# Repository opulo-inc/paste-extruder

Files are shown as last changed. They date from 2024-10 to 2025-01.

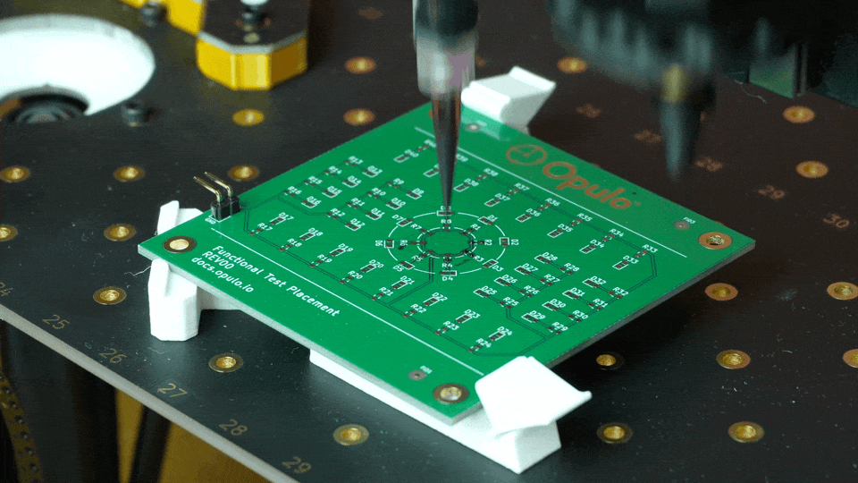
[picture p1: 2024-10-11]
img/hero.gif

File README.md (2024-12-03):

# LumenPnP Paste Extruder

This repository contains the source for a prototype paste extruder head for the LumenPnP.

paste extrusion

**This is a prototype design. It is still in development.**

This extruder head is designed for solder paste and ink dispensing applications. It quickly and easily replaces the right toolhead on any version LumenPnP. It has been used to apply conductive ink and Loctite GC-10 solder paste onto PCBs.

Controlling this toolhead is currently done using `leash`, a python libary for interfacing with the LumenPnP, which can be found [here](https://github.com/opulo-inc/leash). There's an example script in `./sw/extrude/extrude.py` that you can use as a starting point for your own application.

The source CAD for the extruder is designed as a replacement left nozzle. However, the extruder requires a slightly different build of firmware that forces Z homing to occur at a different position, because otherwise the paste extruder will collide with `front-left-leg`. To prevent the extra step of flashing new firmware, the design is mirrored and intended mainly to be used as a replacement *right* nozzle (opposite from the images and YouTube video about this toolhead). If exporting the 3D models yourself, be sure to mirror `extruder-base` and `cartridge-clamp` in your slicer before printing. All other models can be used normally.

## Parts

| Item | Quantity |
| ---- | --- |
| [M3 Nut](https://www.mcmaster.com/90591A250/) | 1 |
| [M3 Threaded Rod](https://www.mcmaster.com/94595A215/) | 1 |
| [Nema 11 Stepper Motor (The higher current rating the better)](https://www.amazon.com/s?k=nema+11+stepper+motor) | 1 |
| [M2.5x5mm Socket Head Bolt](https://www.mcmaster.com/91290A100/) | 4 |
| [M3 Square Nut](https://www.mcmaster.com/97259A101/) | 1 |
| [M3x20mm Socket Head Bolt](https://www.mcmaster.com/91290A123/) | 1 |
| [3ml Luer Lock Syringe](https://www.mcmaster.com/7510A42/) | 1 |
| [Luer Lock Tip (size depends on application)](https://www.mcmaster.com/products/needles/fitting-connection~luer-lock/dispensing-tips-with-luer-lock-connection/tip-type~tapered/) | 1 |

## Install

Installation and setup instructions can be found in this video:

(https://youtu.be/N_p62_QUoKI)

## Help

Feel free to hop in the [LumenPnP Discord Server](https://discordapp.com/invite/TCwy6De ) to help debug and troubleshoot using the extruder head. Also, please feel free to add Github Issues on this repository if you discover any problems.

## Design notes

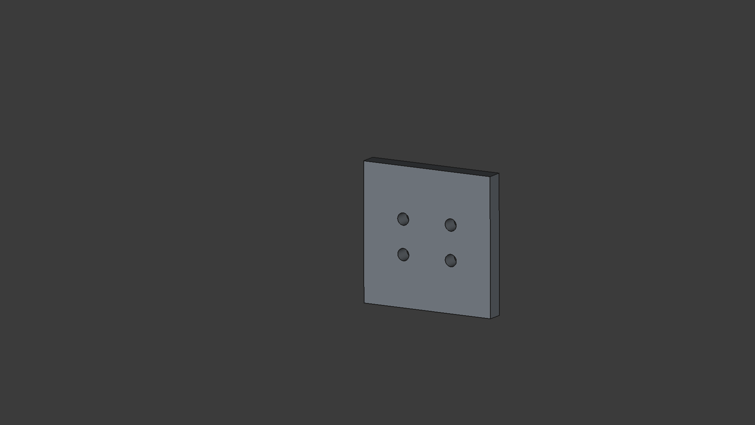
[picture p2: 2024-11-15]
cad/FDM/extruder-base.gif

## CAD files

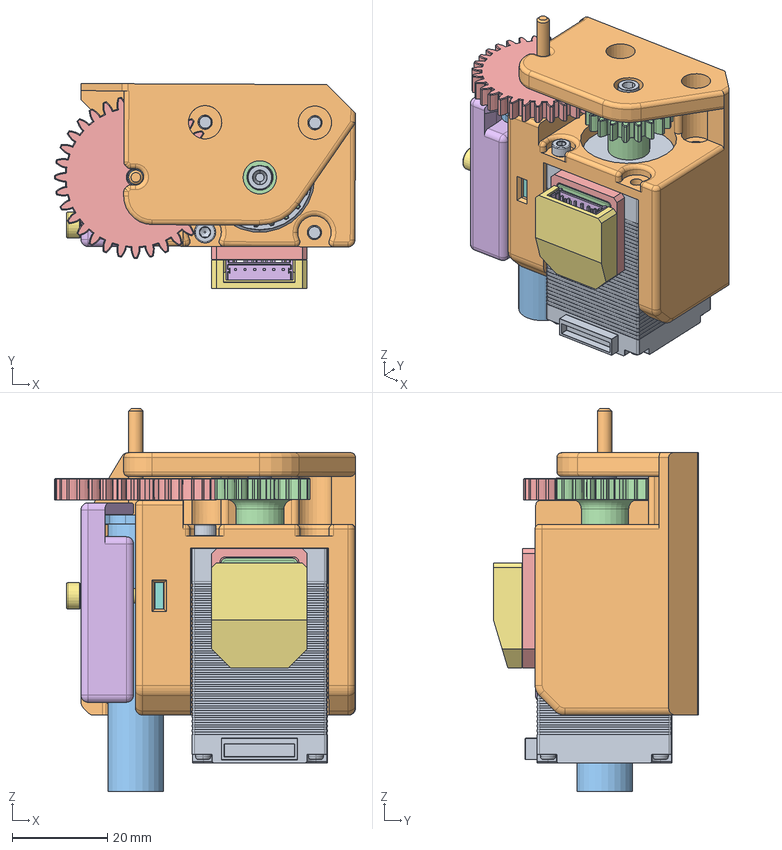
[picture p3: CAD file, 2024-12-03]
cad/subassembly.FCStd
63.1 x 42.9 x 80.2 mm
nema11_001
extruder-base_001
luer_001
extruder-gear_001
cartridge-gear_001
cartridge-clamp_001
M3x20-Screw
M3-Nut
M2.5x5-Screw
M3x70-ThreadedRod
M3-Nut001
stepper-adapter-PCB_001
adapter-mount_001
adapter-cover_001

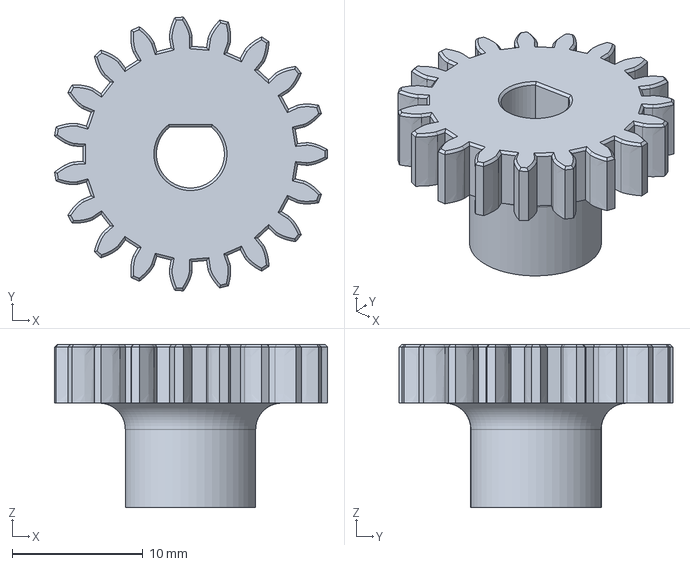
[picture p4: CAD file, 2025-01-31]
cad/FDM/extruder-gear.FCStd
20.9 x 21.0 x 12.5 mm

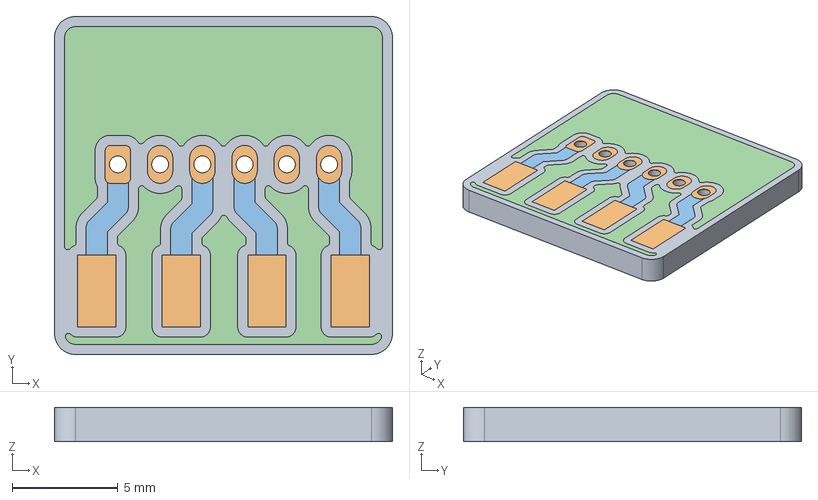
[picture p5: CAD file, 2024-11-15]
cad/OTS/stepper-adapter-PCB.FCStd
16.0 x 16.0 x 1.64 mm
Pcb_5beb
topPads_5beb
topTracks_5beb
topZones_5beb
botPads_5beb
botZones_5beb

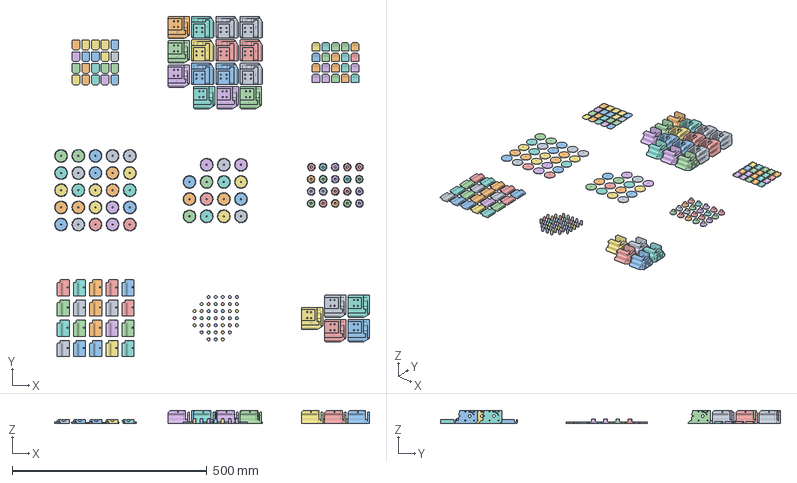
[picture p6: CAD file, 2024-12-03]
mfg/20x-right.3mf
809.3 x 874.3 x 34.0 mm
extruder-base-Body.step x 20
adapter-cover-Body.step x 20
adapter-mount-Body.step x 20
plunger-Body.step x 40
cartridge-clamp-Body.step x 20
extruder-gear-Body.step x 20
cartridge-gear-Body.step 38 x 40

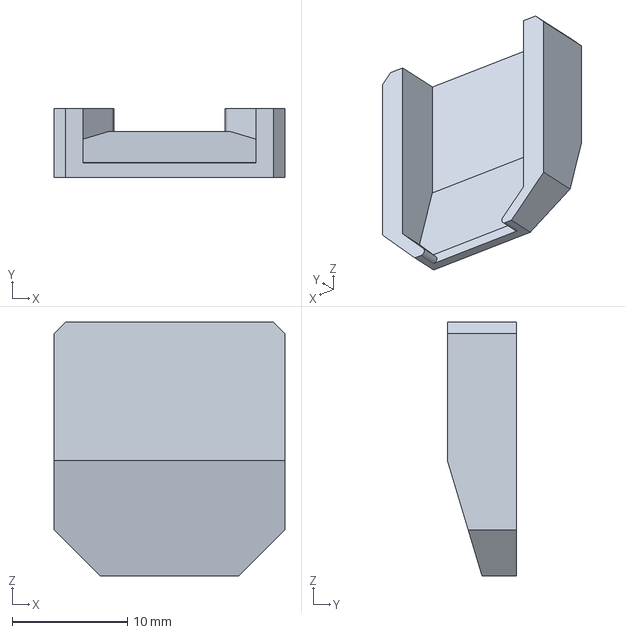
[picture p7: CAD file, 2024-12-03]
cad/FDM/adapter-cover.FCStd
20.0 x 6.00 x 22.0 mm

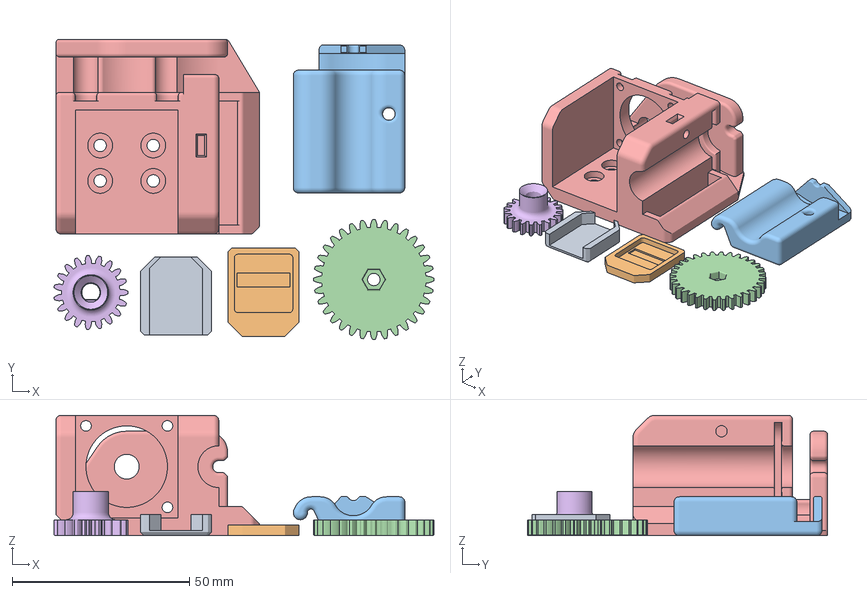
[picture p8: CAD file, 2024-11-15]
mfg/1x-right.3mf
107.3 x 84.8 x 34.0 mm
adapter-cover-Body.step
adapter-mount-Body.step
cartridge-clamp-Body.step
cartridge-gear-Body.step
extruder-base-Body.step
extruder-gear-Body.step

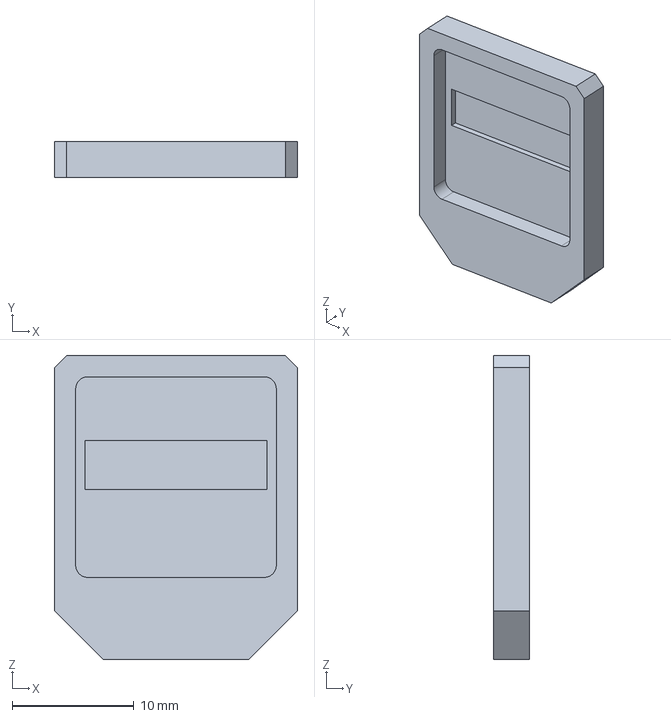
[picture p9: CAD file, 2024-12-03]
cad/FDM/adapter-mount.FCStd
20.0 x 3.00 x 25.0 mm

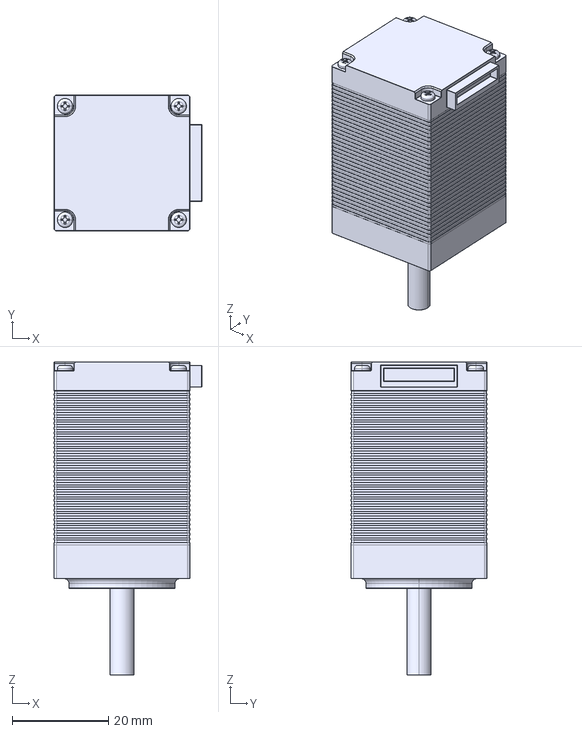
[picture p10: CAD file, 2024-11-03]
cad/OTS/nema11.FCStd
30.7 x 28.2 x 65.0 mm

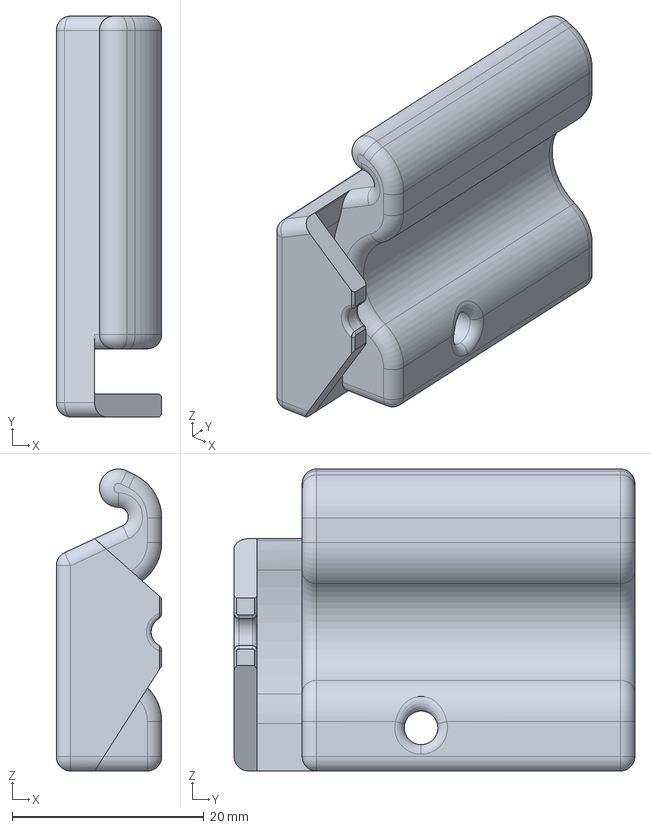
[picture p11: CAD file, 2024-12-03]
cad/FDM/cartridge-clamp.FCStd
11.0 x 41.8 x 31.5 mm

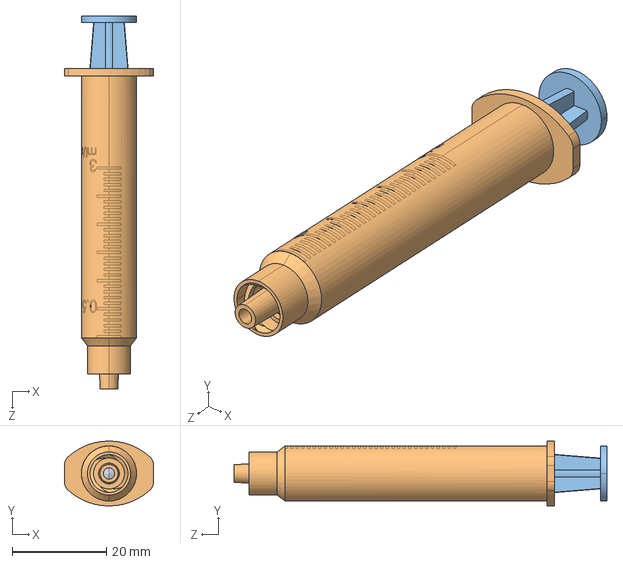
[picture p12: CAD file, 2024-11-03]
cad/OTS/3ml-luer-7510A42.step
18.9 x 13.8 x 79.1 mm

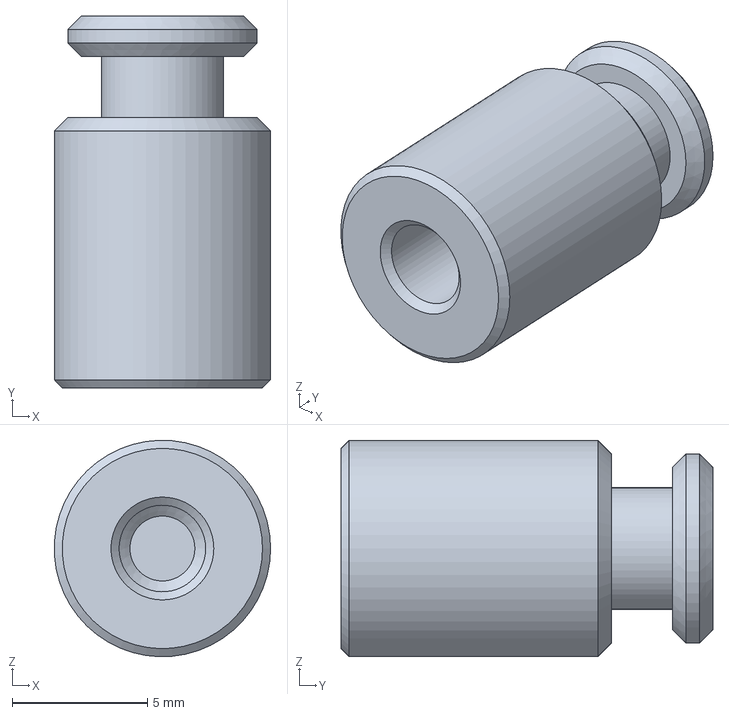
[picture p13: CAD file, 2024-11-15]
cad/FDM/plunger.FCStd
7.99 x 13.8 x 8.00 mm

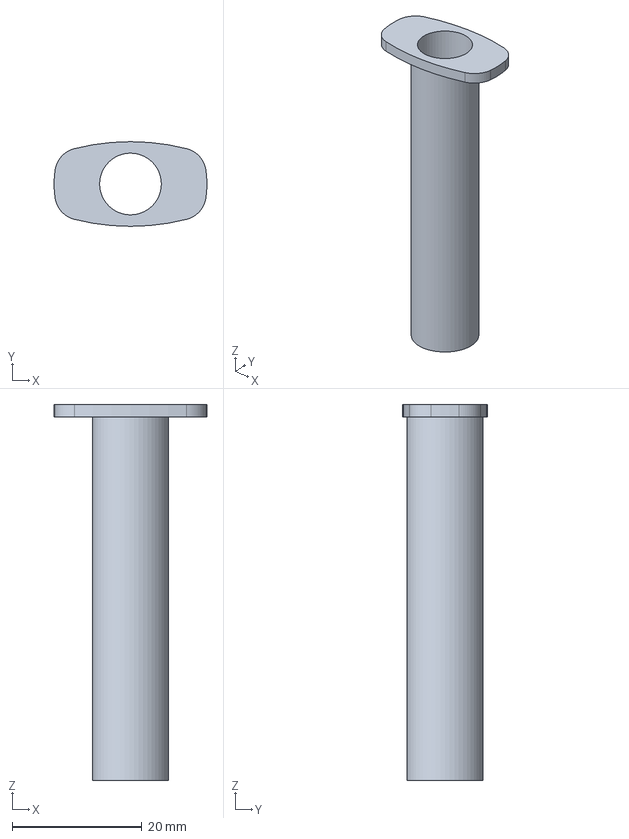
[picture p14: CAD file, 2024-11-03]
cad/OTS/luer.FCStd
23.5 x 13.0 x 57.9 mm

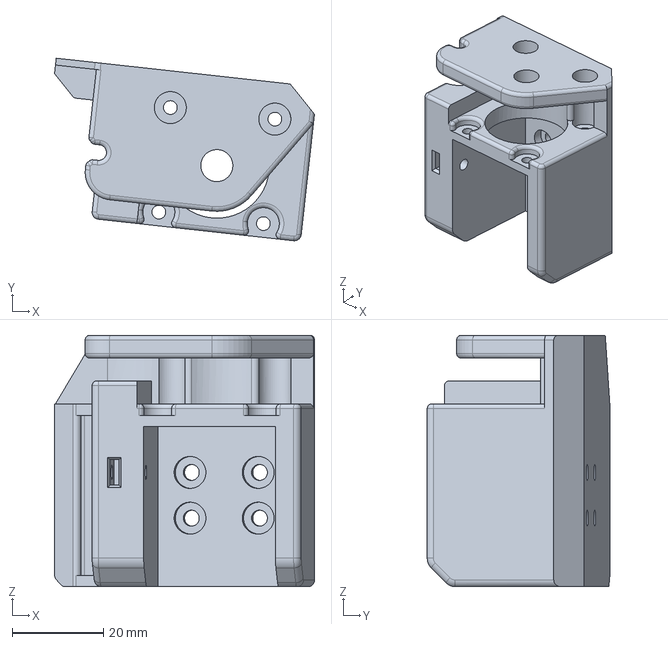
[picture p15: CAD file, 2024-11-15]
cad/FDM/extruder-base.FCStd
56.9 x 39.9 x 55.0 mm

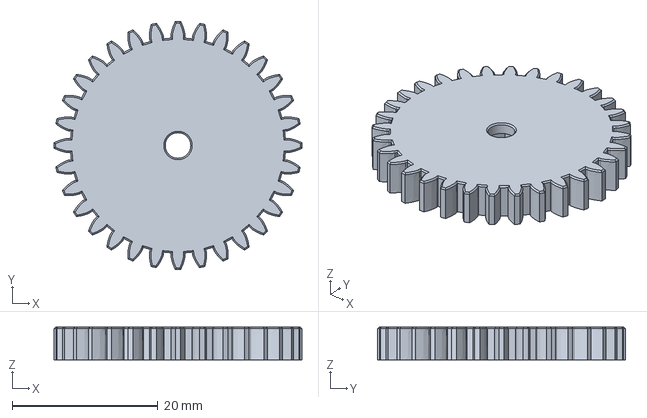
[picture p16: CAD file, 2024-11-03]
cad/FDM/cartridge-gear.FCStd
34.0 x 34.0 x 4.50 mm

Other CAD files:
mfg/1x-left.3mf
cad/OTS/532540670.stp

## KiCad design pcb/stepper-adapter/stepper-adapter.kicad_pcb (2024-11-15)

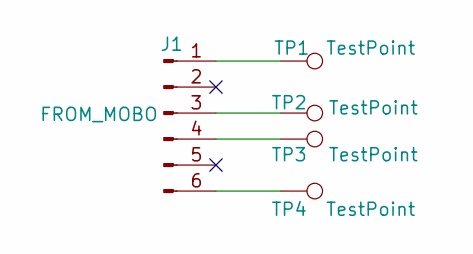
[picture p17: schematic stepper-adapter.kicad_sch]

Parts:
J1: FROM_MOBO; Molex_Micro-Latch_53254-0670_1x06_P2.00mm_Horizontal
TP1, TP2, TP3, TP4: TestPoint; TestPoint_Keystone_5015_Micro-Minature

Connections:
unnamed: J1.1, TP1.1
unnamed: J1.3, TP2.1
unnamed: J1.4, TP3.1
unnamed: J1.6, TP4.1

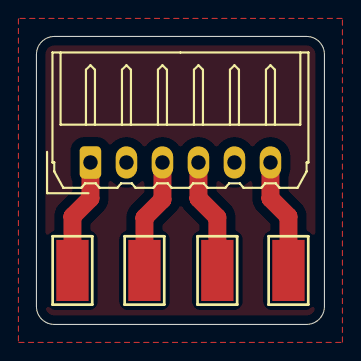
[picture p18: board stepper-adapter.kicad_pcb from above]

Board: 2 copper layers, 16.0 x 16.0 mm, 5 parts (0 on the bottom side), 4 nets.

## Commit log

2024-10-11 fixed bom count of m2 bolt
2024-11-03 restructuring plus github ci test for autobom
    [3ml-luer-7510A42.step, cartridge-clamp.FCStd, cartridge-gear.FCStd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]
2024-11-03 switching back
2024-11-15 bulk commit with paste support
    [1x-left.3mf, 1x-right.3mf, 20x-right.3mf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]
2024-12-03 adds instructions docs
    [20x-right.3mf, adapter-cover.FCStd, adapter-mount.FCStd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]
2025-01-31 loosens extruder-gear shaft fit
    [extruder-gear.FCStd]
